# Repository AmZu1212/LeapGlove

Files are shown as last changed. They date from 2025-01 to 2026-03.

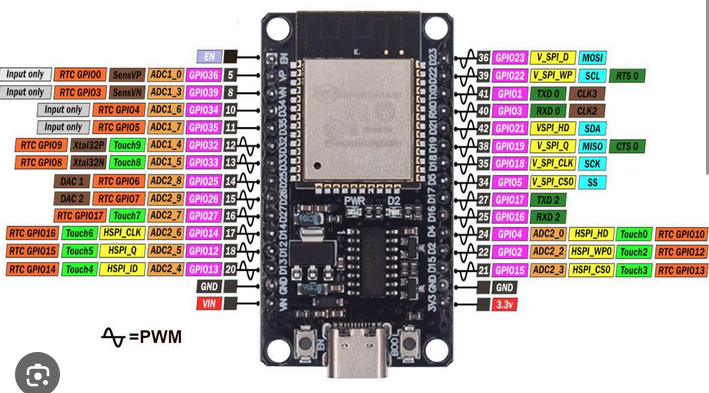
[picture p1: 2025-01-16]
esp pinout.png

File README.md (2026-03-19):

Top Banner
<div align="center">
  <h1>The LeapGlove Project</h1>
  LeapGlove
</div>

## Contact Us
For any questions, feel free to reach out:
- **Emails**: zuabiamir@gmail.com , liz.dushkin@gmail.com
> **Note:** For a complete step-by-step build guide, see the [LeapGlove Wiki Welcome page](https://github.com/AmZu1212/LeapGlove/wiki/%231-Welcome).
  
## Overview
The **LeapGlove Project** aims to repurpose the [LucidGloves](https://github.com/LucidVR/lucidgloves) to control the [LeapHand](https://v1.leaphand.com/) while retaining the haptic feedback capabilities of the glove. 

This initiative focuses on creating an affordable, human-computer interaction interface for the LeapHand.

Watch the showcase here:

Watch the video (https://www.youtube.com/shorts/LX1qnLxFVLc)

The LeapGlove Project builds on:
- **LucidGloves Prototype 4**: [GitHub Repository](https://github.com/LucidVR/lucidgloves)
- **LeapHand API**: [LeapHand Documentation](https://v1.leaphand.com/)

please consider leaving a star on both of the repos above, as without their previous work, this would not be possible.

## Project Objectives
- Repurpose the LucidGloves to function as controllers for the LeapHand.
- Retain the haptic feedback features of the LucidGloves.
- Provide an affordable and accessible solution for LeapHand control.

## Project Status
- This project is finished. We fell abit short of our expected implementation due to the physical design of the mechanism, and due to the latency the servo motors have.
- As a leap hand controller, the gloves supports general finger motion, except fine grain movement and splay movement.
- And for the haptics, it was unfortunately impossible to implement a realtime transmission of haptics, so we created haptic presets from 0% to 90%, so it can be demo'ed if anyone wishes to see how it may feel. 

## Demonstration Videos
- **Glove Demo**:

https://github.com/user-attachments/assets/84f64e34-5cb0-47a1-a268-5b9e06becb94

- **Leap Hand Demo (Courtesy of LeapHand.com)**:

https://github.com/user-attachments/assets/7a54c01e-ebf4-48aa-9cdf-c213115a098e

---

## LeapGlove Assembly & Setup Guide

## Step 1: Complete Hardware List
The hardware needed is listed here, or alternatively you can check lucas'es hadrware list. 
Just be sure to use an `esp32-wroom-32` and not an arduino nano. [Lucas's original parts list](https://github.com/LucidVR/lucidgloves/wiki/Prototype-4-Parts-List)

The Required Hardware:
- 5 black badge reels
- 5 round 10k potentiometers
- 5 mg90s 9g servos
- 1 ESP32-WROOM-32
- 2 small powerbanks (or a power solution of your choice)
- 1 firm-cloth glove (**cloth should not be flexible** for proper haptics)
- Dupont crimp set, crimper, and 28AWG wire kit
- 2 USB-C cables (one for ESP32, one for servos)
- 1 spool of standard PLA/PETG for 3D printing (and a 3D printer)
- 4 M2 bolts and nuts
- Soldering iron and solder
- Foam surface for comfort (to stick under the motor mount base)
- Hot glue gun (even a cheap one will do)
- Some small rope
- A Scotch fishing strap 

> **You will also need a LeapHand already built. See:**  
> [LeapHand Website & CAD Files](https://v1.leaphand.com/leap_cad)

## Step 2: 3D Printing Guide

- Please follow the guide below:  
  [Prototype 4 Printing Guide](https://github.com/LucidVR/lucidgloves/wiki/Prototype-4-Printing-Guide)

- Find the STL files: 
  Navigate to the `lucidglove/3d models` folder in this repository to locate all the required printable parts.  
  > **Note:** Some models differ from the original LucidGlove designs, featuring improvements for print quality and structural strength.

- Check the README in each subfolder:
  Each subfolder contains a `README` file specifying which parts to print and how many of each are needed.

- **Printing Tips:**  
  - Use PLA or PETG for strength and reliability.
  - Recommended infill: at least 20% for durability.
  - Some parts may require supports (snug supports are recommended for all the sliding parts. For the rest use *snug* supports).
  - Test-fit parts before final assembly.

## Step 3: Assembly

Refer to Lucas’s video for a step-by-step assembly:  
Assembly Video (https://www.youtube.com/watch?v=2yF-SJcg3zQ)

**Notes:**
- The majority of the glove’s assembly follows the original LucidGlove design.  
- Use the .stl files we provided (they are more print-friendly than Lucas's designs).
- The motor mounts are designed to be hot glued onto the glove (there is extra space to glue under and on the sides).
- Instead of mounting a Quest2 controller, use the ESP32 mount we provided.

## Step 4: ESP32 Connections

There is flexibility in pin choice if you edit the firmware config.  
This guide assumes you are using the provided firmware as-is (we recommend to not change anything and run as-is).

- The wires should be connected like so:
  
- The finished product should look like this:
  
  
## Step 5: Setting Up the Code

1. **Download CH340 USB drivers:**  
   - [CH340 driver link here](https://sparks.gogo.co.nz/ch340.html)
   - please not that maybe your esp wil have a cp210 driver instead, just install that one.
   - The driver type depends on the small chip near the usb port on the esp board.

2. **Install drivers** and connect your ESP32 board via USB.

3. **Open Windows Device Manager:**
    - Right click the Windows icon  
      
    - Choose Device Manager  
      

    - Find your “CH340” COM device under Ports (COM & LPT). (For us it is COM3, but for you the number may be different) 
      

4. **Download and install Arduino IDE.**  
   Follow Lucas’s video for preparation and board profile setup (use the updated firmware):  
   [Lucas's Arduino Prep Video](https://www.youtube.com/watch?v=2yF-SJcg3zQ)

5. **Compile and program the ESP32.**

6. **Connect the electronics and pair the LeapGlove with Windows via Bluetooth:**
    - Open your PC’s Bluetooth panel and pair with the LeapGlove.
    - Check in device manager which COM# is your esp bluetooth connection:

      
      
    - Update the esp port in the script:
      

## Step 6: How to Wear and Use the Glove Safely

- **Tension will differ per user.**
- **You must:**  
  - Re-tighten the ropes  
  - Adjust the servo motor’s tail

### Rope and Servo Adjustment Procedure

1. Remove all 5 tails from the servos.
2. Run the script, press `Ctrl+C`, and wait for calibration to finish.
3. Press `0` to reset servo positions to zero.  
   Close the script.
4. Tighten and spin the ropes on each finger cap handle.
    - Ensure there is tension even when the hand is fully open.
5. Close your hand.
6. For each motor, one by one, put the tail on **after** (clockwise) the screw position.  
   This sets the motor’s “zero” point. Please refer to the image and gif below:
   
   Motor Tail Placement

   GIF of how it should look like:
   
   Motor Tail Placement GIF

### Operation Safety

- **Always have your hand fully open when changing haptic presets.**  
  - Not doing so may cause the servo tail to hit the brake screw and dislodge it, ruining the haptic mechanism.
- **If you have tracking issues:**  
  - Ropes aren’t tight enough. Re-tighten and recalibrate.
- **If you have haptics issues (servos don’t stop hand movement):**  
  - Glove material is too flexible, or servos are misaligned. Re-align as above.

### Final Steps

- **LeapHand Setup:**  
  Build and connect the LeapHand to your PC following the [LeapHand documentation](https://v1.leaphand.com/).

- **Software:**  
  Once hardware is ready and connected (if used bluetooth dont forget to pair to the LeapGlove), run the integration script for the `Our Files` Folder:
  ```
  python ./LeapGlove.py
  ```

Bottom Banner

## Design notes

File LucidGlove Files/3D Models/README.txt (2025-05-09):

Hello!

Check each folder for what you need to print.
Open "#Print Guide.txt" and check the list and the instructions.

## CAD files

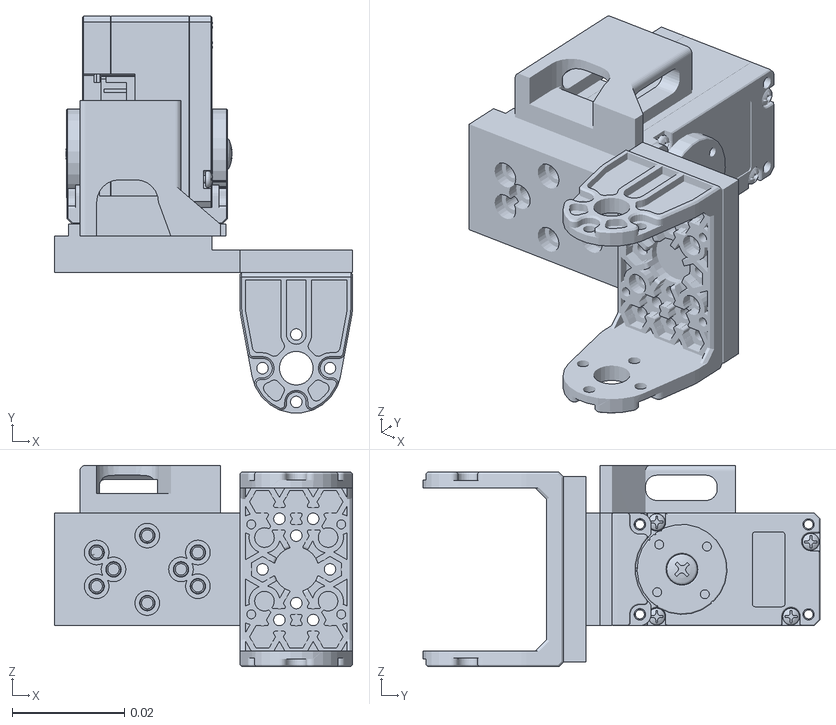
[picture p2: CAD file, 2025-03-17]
LeapHand Files/LeapHand Simulator/assets/leap_hand/mcp_joint.stl
0.053 x 0.0705 x 0.0358

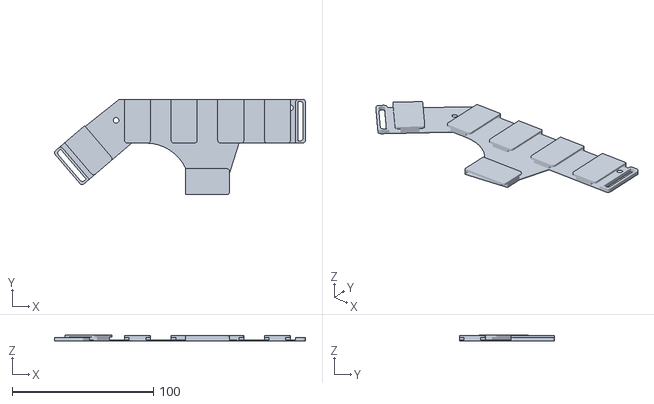
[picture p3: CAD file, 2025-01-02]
LucidGlove Files/3D Models/Base/Right_Hand_Base.stl
177.7 x 67.6 x 4.60

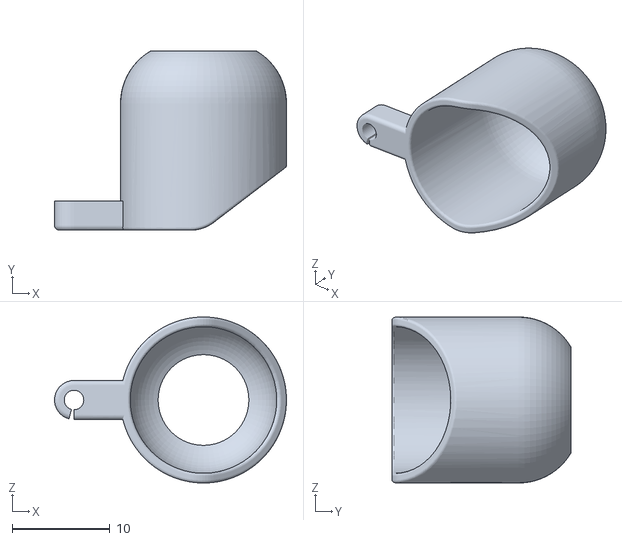
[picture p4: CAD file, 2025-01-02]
LucidGlove Files/3D Models/Fingers/Finger_Cap.stl
23.8 x 18.4 x 17.0

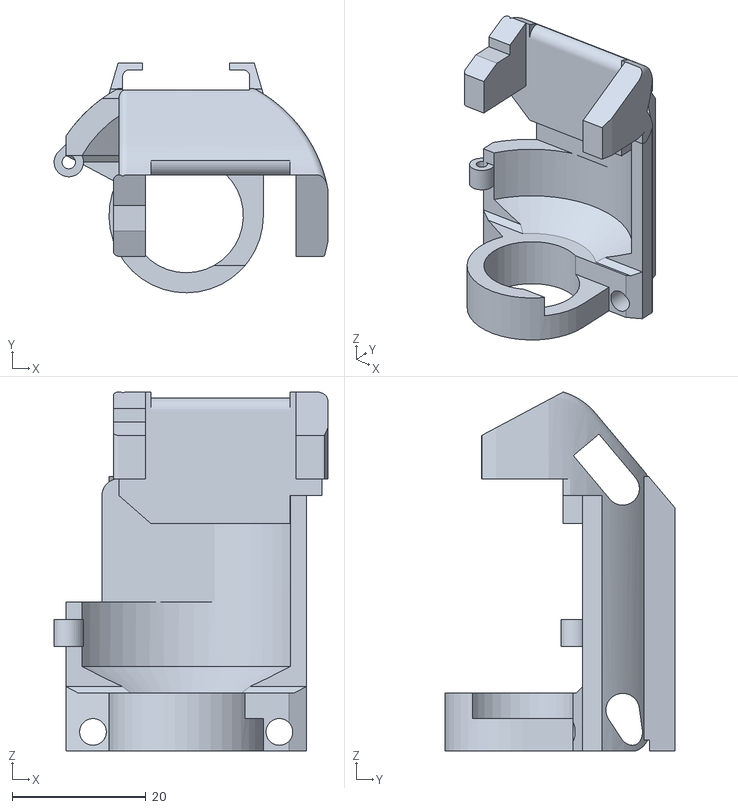
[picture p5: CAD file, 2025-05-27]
LucidGlove Files/3D Models/Mounts/Motor_Mount.stl
41.0 x 34.3 x 53.7

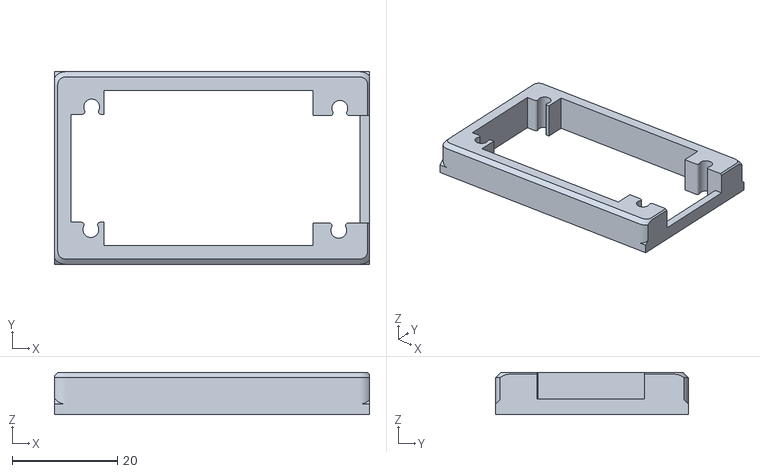
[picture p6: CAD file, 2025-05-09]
LucidGlove Files/3D Models/Mounts/Mount Source Files/ESP_Bracket.stl
59.8 x 36.6 x 8.00

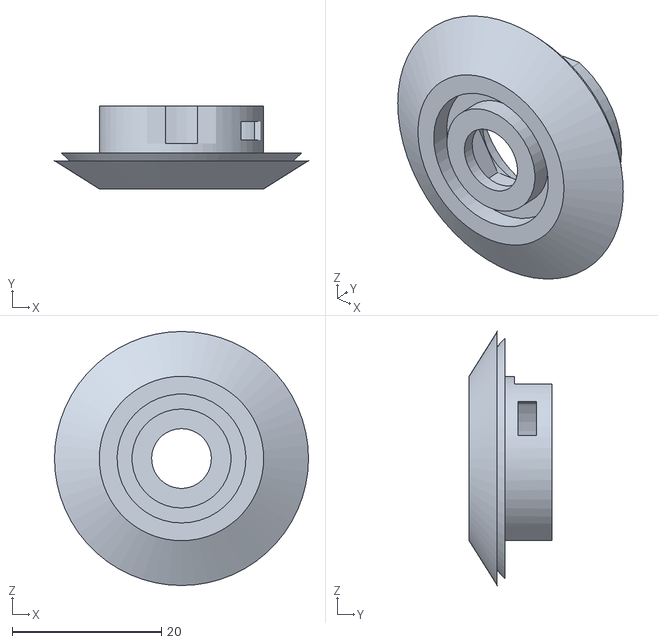
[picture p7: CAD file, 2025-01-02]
LucidGlove Files/3D Models/Spool & Coil/Coil_Holder.stl
34.0 x 11.1 x 34.0

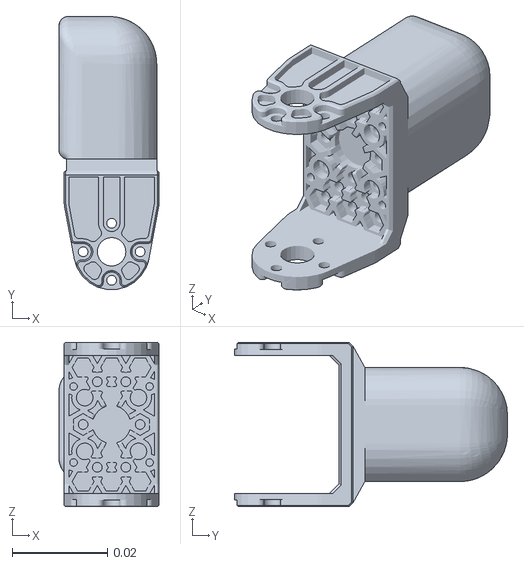
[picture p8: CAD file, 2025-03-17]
LeapHand Files/LeapHand Simulator/assets/leap_hand/fingertip.stl
0.0211 x 0.0574 x 0.0346

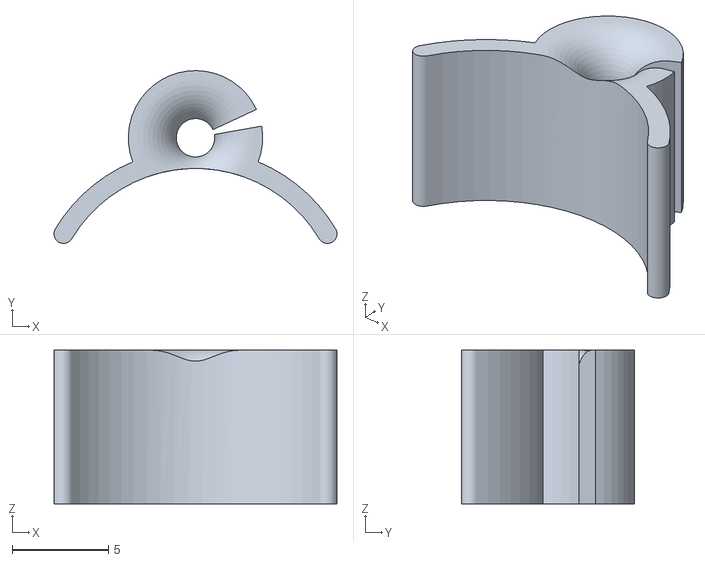
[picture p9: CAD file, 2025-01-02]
LucidGlove Files/3D Models/Fingers/String_Guide.stl
14.7 x 9.00 x 8.00

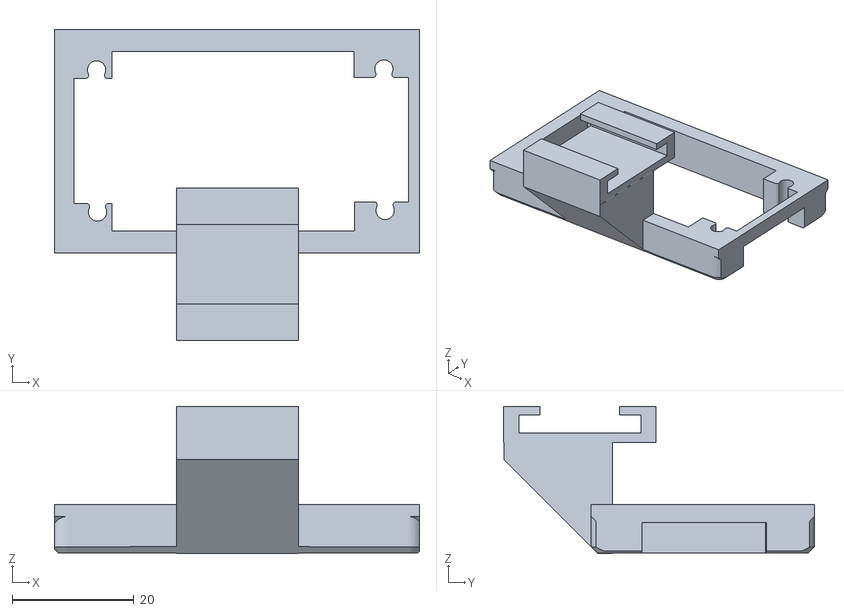
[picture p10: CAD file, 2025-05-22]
LucidGlove Files/3D Models/Mounts/ESP_Mount.stl
59.8 x 50.9 x 24.2

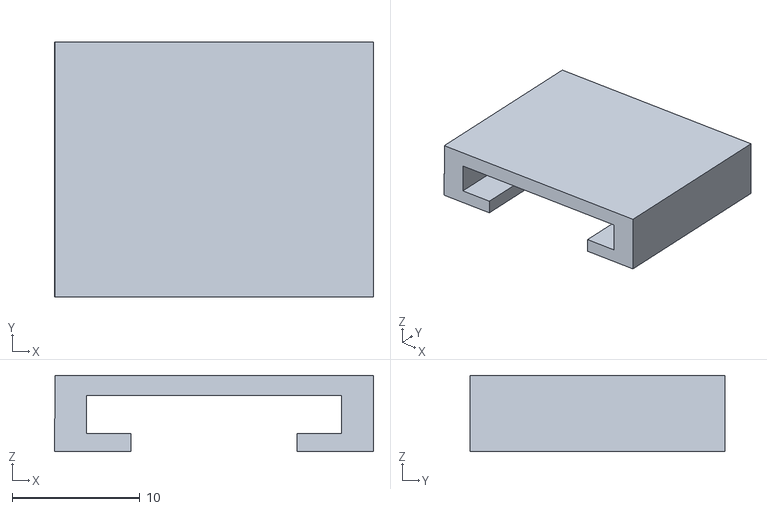
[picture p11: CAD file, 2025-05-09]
LucidGlove Files/3D Models/Mounts/Mount Source Files/Mount_Slide.stl
25.0 x 20.0 x 5.97

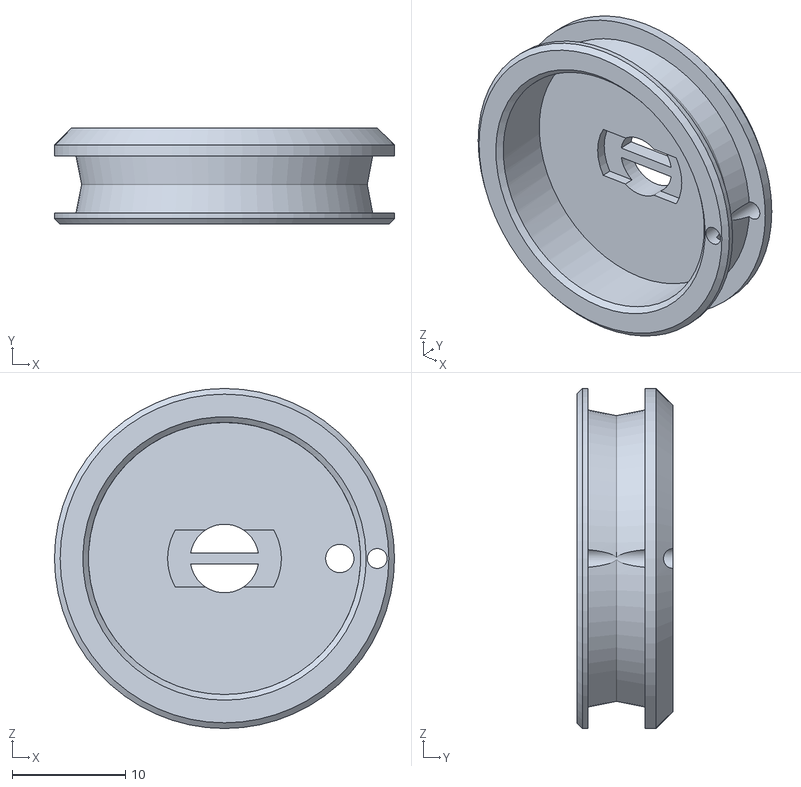
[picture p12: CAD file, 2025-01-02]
LucidGlove Files/3D Models/Spool & Coil/String_Spool.stl
30.0 x 8.50 x 30.0

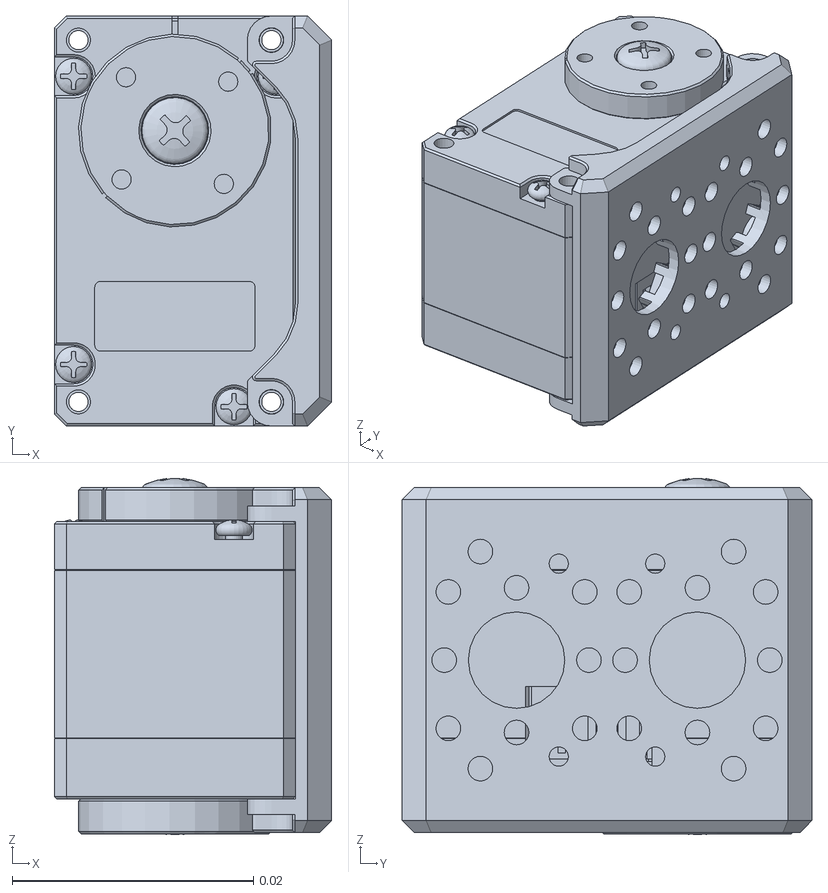
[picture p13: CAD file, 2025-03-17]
LeapHand Files/LeapHand Simulator/assets/leap_hand/pip.stl
0.023 x 0.034 x 0.0295

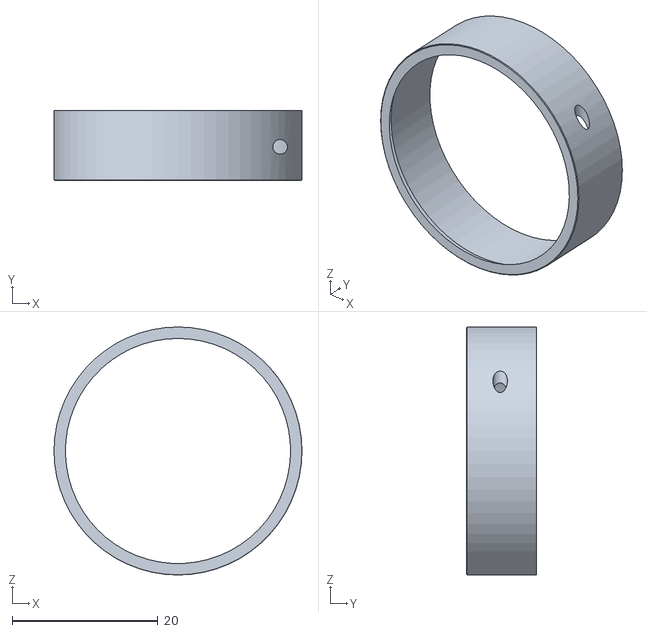
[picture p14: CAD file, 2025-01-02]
LucidGlove Files/3D Models/Spool & Coil/Spool_Ring.stl
34.0 x 9.63 x 34.0

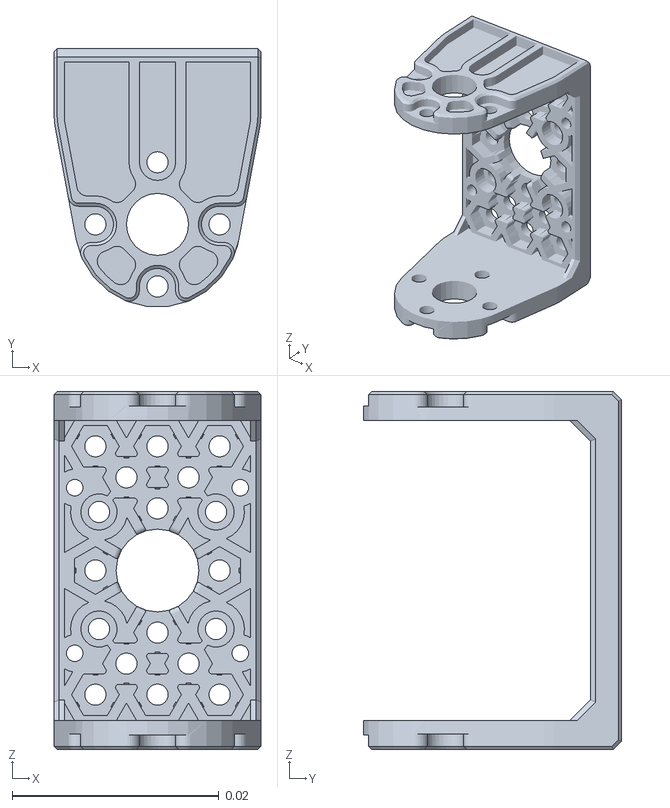
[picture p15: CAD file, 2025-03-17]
LeapHand Files/LeapHand Simulator/assets/leap_hand/thumb_pip.stl
0.02 x 0.0249 x 0.0346

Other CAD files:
LucidGlove Files/3D Models/Base/Left_Hand_Base.stl
LucidGlove Files/3D Models/Mounts/Mount Source Files/Motor_Mount.stl
LeapHand Files/LeapHand Simulator/assets/leap_hand/thumb_dip.stl
LeapHand Files/LeapHand Simulator/assets/leap_hand/dip.stl
LeapHand Files/LeapHand Simulator/assets/leap_hand/thumb_fingertip.stl
LucidGlove Files/3D Models/Mounts/Mount Source Files/Old_ESP_Mount.stl

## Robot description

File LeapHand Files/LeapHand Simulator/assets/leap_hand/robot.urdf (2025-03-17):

<robot name="onshape">
<link name="palm_lower">
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
<inertial>
<origin xyz="0 0 0" rpy="0 0 0"/>
<mass value="0.237" />
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
</inertial>
</link>

<link name="mcp_joint">
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
<inertial>
<origin xyz="0 0 0" rpy="0 0 0"/>
<mass value="0.044" />
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
</inertial>
</link>

<link name="pip">
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
<inertial>
<origin xyz="0 0 0" rpy="0 0 0"/>
<mass value="0.032" />
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
</inertial>
</link>

<link name="dip">
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
<inertial>
<origin xyz="0 0 0" rpy="0 0 0"/>
<mass value="0.037" />
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
</inertial>
</link>

<link name="fingertip">
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
<inertial>
<origin xyz="0 0 0" rpy="0 0 0"/>
<mass value="0.016" />
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
</inertial>
</link>

<joint name="0" type="revolute">
<origin xyz="-0.012200000000000007713 0.038099999999999994982 0.014500000000000000736" rpy="-1.570796326794896558 -1.0065212660796336576e-15 1.5707963267948943376" />
<parent link="mcp_joint" />
<child link="pip" />
<axis xyz="0 0 -1"/>
<limit effort="0.95" velocity="8.48" lower = "-1.047" upper = "1.047"/>
<joint_properties friction="0.0"/>
</joint>

<joint name="1" type="revolute">
<origin xyz="-0.0070952496528625457958 0.023057756134899472233 -0.01872240357846021927" rpy="1.5707963267948950037 1.5707963267948945596 0" />
<parent link="palm_lower" />
<child link="mcp_joint" />
<axis xyz="0 0 -1"/>
<limit effort="0.95" velocity="8.48" lower = "-0.314" upper = "2.23"/>
<joint_properties friction="0.0"/>
</joint>

<joint name="2" type="revolute">
<origin xyz="0.01499999999999996822 0.014299999999999904801 -0.012999999999999824196" rpy="1.5707963267948958919 -1.570796326794896336 0" />
<parent link="pip" />
<child link="dip" />
<axis xyz="0 0 -1"/>
<limit effort="0.95" velocity="8.48" lower = "-0.506" upper = "1.885"/>  
<joint_properties friction="0.0"/>
</joint>

<joint name="3" type="revolute">
<origin xyz="-4.0880582495572692636e-09 -0.036100004210367367397 0.00020000000000007858714" rpy="4.5935029425113685044e-17 -2.8730071914463794583e-16 4.4395481053923607589e-32" />
<parent link="dip" />
<child link="fingertip" />
<axis xyz="0 0 -1"/>
<limit effort="0.95" velocity="8.48" lower = "-0.366" upper = "2.042"/>   
<joint_properties friction="0.0"/>
</joint>

<link name="mcp_joint_2">
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
<inertial>
<origin xyz="0 0 0" rpy="0 0 0"/>
<mass value="0.044" />
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
</inertial>
</link>

<link name="pip_2">
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
<inertial>
<origin xyz="0 0 0" rpy="0 0 0"/>
<mass value="0.032" />
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
</inertial>
</link>

<link name="dip_2">
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
<inertial>
<origin xyz="0 0 0" rpy="0 0 0"/>
<mass value="0.037" />
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
</inertial>
</link>

<link name="fingertip_2">
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
<inertial>
<origin xyz="0 0 0" rpy="0 0 0"/>
<mass value="0.016" />
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
</inertial>
</link>

<joint name="4" type="revolute">
<origin xyz="-0.012200000000000019856 0.038099999999999981104 0.01450000000000000594" rpy="-1.570796326794896558 -1.0065212760057939085e-15 1.5707963267948943376" />
<parent link="mcp_joint_2" />
<child link="pip_2" />
<axis xyz="0 0 -1"/>
<limit effort="0.95" velocity="8.48" lower = "-1.047" upper = "1.047"/>
<joint_properties friction="0.0"/>
</joint>

<joint name="5" type="revolute">
<origin xyz="-0.0070952496528625388569 -0.022392243865100525113 -0.018722403578460229678" rpy="1.570796326794896558 1.570796326794896558 0" />
<parent link="palm_lower" />
<child link="mcp_joint_2" />
<axis xyz="0 0 -1"/>
<limit effort="0.95" velocity="8.48" lower = "-0.314" upper = "2.23"/>
<joint_properties friction="0.0"/>
</joint>

<joint name="6" type="revolute">
<origin xyz="0.014999999999999975159 0.014300000000000000211 -0.013000000000000018485" rpy="1.5707963267948958919 -1.570796326794896336 0" />
<parent link="pip_2" />
<child link="dip_2" />
<axis xyz="0 0 -1"/>
<limit effort="0.95" velocity="8.48" lower = "-0.506" upper = "1.885"/>  
<joint_properties friction="0.0"/>
</joint>

<joint name="7" type="revolute">
<origin xyz="1.0061396160665481148e-16 -0.036099999999999854428 0.00020000000000007858714" rpy="4.5935029425113654229e-17 -2.8730071914463794583e-16 1.4408183216511868558e-31" />
<parent link="dip_2" />
<child link="fingertip_2" />
<axis xyz="0 0 -1"/>
<limit effort="0.95" velocity="8.48" lower = "-0.366" upper = "2.042"/>   
<joint_properties friction="0.0"/>
</joint>

<link name="mcp_joint_3">
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
<inertial>
<origin xyz="0 0 0" rpy="0 0 0"/>
<mass value="0.044" />
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
</inertial>
</link>

<link name="pip_3">
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
<inertial>
<origin xyz="0 0 0" rpy="0 0 0"/>
<mass value="0.032" />
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
</inertial>
</link>

<link name="dip_3">
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
<inertial>
<origin xyz="0 0 0" rpy="0 0 0"/>
<mass value="0.037" />
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
</inertial>
</link>

<link name="fingertip_3">
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
<inertial>
<origin xyz="0 0 0" rpy="0 0 0"/>
<mass value="0.016" />
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
</inertial>
</link>

<joint name="8" type="revolute">
<origin xyz="-0.012200000000000004244 0.038100000000000001921 0.014499999999999999001" rpy="-1.570796326794896558 -1.0065212660796360242e-15 1.5707963267948943376" />
<parent link="mcp_joint_3" />
<child link="pip_3" />
<axis xyz="0 0 -1"/>
<limit effort="0.95" velocity="8.48" lower = "-1.047" upper = "1.047"/>
<joint_properties friction="0.0"/>
</joint>

<joint name="9" type="revolute">
<origin xyz="-0.0070952454426398371343 -0.067842243865100515521 -0.018722407666402932774" rpy="1.5707963267948950037 1.5707963267948945596 0" />
<parent link="palm_lower" />
<child link="mcp_joint_3" />
<axis xyz="0 0 -1"/>
<limit effort="0.95" velocity="8.48" lower = "-0.314" upper = "2.23"/>
<joint_properties friction="0.0"/>
</joint>

<joint name="10" type="revolute">
<origin xyz="0.014999999999999971689 0.014299999999999951639 -0.012999999999999959505" rpy="1.5707963267948958919 -1.570796326794896336 0" />
<parent link="pip_3" />
<child link="dip_3" />
<axis xyz="0 0 -1"/>
<limit effort="0.95" velocity="8.48" lower = "-0.506" upper = "1.885"/>  
<joint_properties friction="0.0"/>
</joint>

<joint name="11" type="revolute">
<origin xyz="9.7144514654701197287e-17 -0.036099999999999868305 0.00020000000000007511769" rpy="4.5935029425113685044e-17 -2.8730071914463799514e-16 1.5565411607615035382e-32" />
<parent link="dip_3" />
<child link="fingertip_3" />
<axis xyz="0 0 -1"/>
<limit effort="0.95" velocity="8.48" lower = "-0.366" upper = "2.042"/>   
<joint_properties friction="0.0"/>
</joint>

<link name="pip_4">
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
<inertial>
<origin xyz="0 0 0" rpy="0 0 0"/>
<mass value="0.032" />
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
</inertial>
</link>

<link name="thumb_pip">
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
<inertial>
<origin xyz="0 0 0" rpy="0 0 0"/>
<mass value="0.003" />
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
</inertial>
</link>

<link name="thumb_dip">
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
<inertial>
<origin xyz="0 0 0" rpy="0 0 0"/>
<mass value="0.038" />
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
</inertial>
</link>

<link name="thumb_fingertip">
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
<inertial>
<origin xyz="0 0 0" rpy="0 0 0"/>
<mass value="0.049" />
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
</inertial>
</link>

<joint name="12" type="revolute">
<origin xyz="-0.069395249652862533996 -0.0012422438651005258004 -0.021622403578460215601" rpy="-8.2381766464939424156e-17 1.5707963267948956698 0" />
<parent link="palm_lower" />
<child link="pip_4" />
<axis xyz="0 0 -1"/>
<limit effort="0.95" velocity="8.48" lower = "-0.349" upper = "2.094"/> 
<joint_properties friction="0.0"/>
</joint>

<joint name="13" type="revolute">
<origin xyz="-2.7755575615628913511e-17 0.014300000000000005415 -0.013000000000000011546" rpy="1.5707963267948958919 -1.570796326794896336 0" />
<parent link="pip_4" />
<child link="thumb_pip" />
<axis xyz="0 0 -1"/>
<limit effort="0.95" velocity="8.48" lower = "-0.47" upper = "2.443"/> 
<joint_properties friction="0.0"/>
</joint>

<joint name="14" type="revolute">
<origin xyz="0 0.014499999999999966041 -0.017000000000000053263" rpy="-1.570796326794896558 1.6050198443300131245e-46 -1.9721522630516624601e-31" />
<parent link="thumb_pip" />
<child link="thumb_dip" />
<axis xyz="0 0 -1"/>
<limit effort="0.95" velocity="8.48" lower = "-1.20" upper = "1.90"/> 
<joint_properties friction="0.0"/>
</joint>
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

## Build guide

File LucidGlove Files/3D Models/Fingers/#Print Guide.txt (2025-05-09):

Print:

9x String_Guide.stl
5x Finger_Cap.stl

Re-size Finger_Cap.stl to fit each of your fingers. Play with the scale.

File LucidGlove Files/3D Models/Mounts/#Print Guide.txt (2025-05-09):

Print:

5x Motor_Mount.stl
1x ESP_Mount.stl

You can ignore the "Mount Source Files" folder.

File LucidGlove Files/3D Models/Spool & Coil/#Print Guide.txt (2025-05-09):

Print:

5x Coil_Holder.stl
5x Spool_Ring.stl
5x String_Spool.stl

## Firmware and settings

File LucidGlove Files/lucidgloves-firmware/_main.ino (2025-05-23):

#define ALWAYS_CALIBRATING CALIBRATION_LOOPS == -1

#define CALIB_OVERRIDE false
#if USING_CALIB_PIN && COMMUNICATION == COMM_SERIAL && PIN_CALIB == 0 && !CALIB_OVERRIDE
#error "You can't set your calibration pin to 0 over usb. You can calibrate with the BOOT button when using bluetooth only. Set CalibOverride to true to override this."
#endif

ICommunication* comm;
int loops = 0;
void setup() {
#if COMMUNICATION == COMM_SERIAL
  comm = new SerialCommunication();
#elif COMMUNICATION == COMM_BTSERIAL
  comm = new BTSerialCommunication();
#endif
  comm->start();

  setupInputs();

#if USING_FORCE_FEEDBACK
  setupServoHaptics();
#endif
}

void loop() {
  if (comm->isOpen()) {
#if USING_CALIB_PIN
    bool calibButton = getButton(PIN_CALIB) != INVERT_CALIB;
    if (calibButton)
      loops = 0;
#else
    bool calibButton = false;
#endif

    bool calibrate = false;
    if (loops < CALIBRATION_LOOPS || ALWAYS_CALIBRATING) {
      calibrate = true;
      loops++;
    }

    int* fingerPos = getFingerPositions(calibrate, calibButton);
    bool joyButton = getButton(PIN_JOY_BTN) != INVERT_JOY;

#if TRIGGER_GESTURE
    bool triggerButton = triggerGesture(fingerPos);
#else
    bool triggerButton = getButton(PIN_TRIG_BTN) != INVERT_TRIGGER;
#endif

    bool aButton = getButton(PIN_A_BTN) != INVERT_A;
    bool bButton = getButton(PIN_B_BTN) != INVERT_B;

#if GRAB_GESTURE
    bool grabButton = grabGesture(fingerPos);
#else
    bool grabButton = getButton(PIN_GRAB_BTN) != INVERT_GRAB;
#endif

#if PINCH_GESTURE
    bool pinchButton = pinchGesture(fingerPos);
#else
    bool pinchButton = getButton(PIN_PNCH_BTN) != INVERT_PINCH;
    z
#endif

    bool menuButton = getButton(PIN_MENU_BTN) != INVERT_MENU;

    comm->output(encode(fingerPos, getJoyX(), getJoyY(), joyButton, triggerButton, aButton, bButton, grabButton, pinchButton, calibButton, menuButton));
    #if USING_FORCE_FEEDBACK
    static unsigned long lastHapticTime = 0;
    const unsigned long hapticInterval = 15;  // ~66 Hz

    char received[50];
    if (comm->available() && millis() - lastHapticTime > hapticInterval) {
      if (comm->readData(received)) {
        int hapticLimits[5];
        decodeData(received, hapticLimits);
        writeServoHaptics(hapticLimits);
        lastHapticTime = millis();
      }
    }
#endif
    delay(LOOP_TIME);
  }
}

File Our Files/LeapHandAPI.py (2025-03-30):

import numpy as np

from leap_hand_utils.dynamixel_client import *
import leap_hand_utils.leap_hand_utils as lhu
import time
#######################################################
"""This can control and query the LEAP Hand

I recommend you only query when necessary and below 90 samples a second.  Used the combined commands if you can to save time.  Also don't forget about the USB latency settings in the readme.

#Allegro hand conventions:
#0.0 is the all the way out beginning pose, and it goes positive as the fingers close more and more.

#LEAP hand conventions:
#180 is flat out home pose for the index, middle, ring, finger MCPs.
#Applying a positive angle closes the joints more and more to curl closed.
#The MCP is centered at 180 and can move positive or negative to that.

#The joint numbering goes from Index (0-3), Middle(4-7), Ring(8-11) to Thumb(12-15) and from MCP Side, MCP Forward, PIP, DIP for each finger.
#For instance, the MCP Side of Index is ID 0, the MCP Forward of Ring is 9, the DIP of Ring is 11

"""
########################################################
class LeapNode:
    def __init__(self):
        ####Some parameters
        # I recommend you keep the current limit from 350 for the lite, and 550 for the full hand
        # Increase KP if the hand is too weak, decrease if it's jittery.
        self.kP = 600
        self.kI = 0
        self.kD = 200
        self.curr_lim = 350
        self.prev_pos = self.pos = self.curr_pos = lhu.allegro_to_LEAPhand(np.zeros(16))
        #You can put the correct port here or have the node auto-search for a hand at the first 3 ports.
        # For example ls /dev/serial/by-id/* to find your LEAP Hand. Then use the result.  
        # For example: /dev/serial/by-id/usb-FTDI_USB__-__Serial_Converter_FT7W91VW-if00-port0
        self.motors = motors = [0,1,2,3,4,5,6,7,8,9,10,11,12,13,14,15]
        try:
            self.dxl_client = DynamixelClient(motors, '/dev/ttyUSB0', 4000000)
            self.dxl_client.connect()
        except Exception:
            try:
                self.dxl_client = DynamixelClient(motors, '/dev/ttyUSB1', 4000000)
                self.dxl_client.connect()
            except Exception:
                self.dxl_client = DynamixelClient(motors, 'COM5', 4000000)
                self.dxl_client.connect()
        #Enables position-current control mode and the default parameters, it commands a position and then caps the current so the motors don't overload
        self.dxl_client.sync_write(motors, np.ones(len(motors))*5, 11, 1)
        self.dxl_client.set_torque_enabled(motors, True)
        self.dxl_client.sync_write(motors, np.ones(len(motors)) * self.kP, 84, 2) # Pgain stiffness     
        self.dxl_client.sync_write([0,4,8], np.ones(3) * (self.kP * 0.75), 84, 2) # Pgain stiffness for side to side should be a bit less
        self.dxl_client.sync_write(motors, np.ones(len(motors)) * self.kI, 82, 2) # Igain
        self.dxl_client.sync_write(motors, np.ones(len(motors)) * self.kD, 80, 2) # Dgain damping
        self.dxl_client.sync_write([0,4,8], np.ones(3) * (self.kD * 0.75), 80, 2) # Dgain damping for side to side should be a bit less
        #Max at current (in unit 1ma) so don't overheat and grip too hard #500 normal or #350 for lite
        self.dxl_client.sync_write(motors, np.ones(len(motors)) * self.curr_lim, 102, 2)
        self.dxl_client.write_desired_pos(self.motors, self.curr_pos)

    #Receive LEAP pose and directly control the robot
    def set_leap(self, pose):
        self.prev_pos = self.curr_pos
        self.curr_pos = np.array(pose)
        self.dxl_client.write_desired_pos(self.motors, self.curr_pos)
    #allegro compatibility joint angles.  It adds 180 to make the fully open position at 0 instead of 180
    def set_allegro(self, pose):
        pose = lhu.allegro_to_LEAPhand(pose, zeros=False)
        self.prev_pos = self.curr_pos
        self.curr_pos = np.array(pose)
        self.dxl_client.write_desired_pos(self.motors, self.curr_pos)
    #Sim compatibility for policies, it assumes the ranges are [-1,1] and then convert to leap hand ranges.
    def set_ones(self, pose):
        pose = lhu.sim_ones_to_LEAPhand(np.array(pose))
        self.prev_pos = self.curr_pos
        self.curr_pos = np.array(pose)
        self.dxl_client.write_desired_pos(self.motors, self.curr_pos)
    #read position of the robot
    def read_pos(self):
        return self.dxl_client.read_pos()
    #read velocity
    def read_vel(self):
        return self.dxl_client.read_vel()
    #read current
    def read_cur(self):
        return self.dxl_client.read_cur()
    #These combined commands are faster FYI and return a list of data
    def pos_vel(self):
        return self.dxl_client.read_pos_vel()
    #These combined commands are faster FYI and return a list of data
    def pos_vel_eff_srv(self):
        return self.dxl_client.read_pos_vel_cur()
########################################################


#init the node
def main(**kwargs):
    leap_hand = LeapNode()
    while True:
        #Set to an open pose and read the joint angles 33hz
        leap_hand.set_allegro(np.zeros(16))
        print("Position: " + str(leap_hand.read_pos()))
        time.sleep(0.03)

if __name__ == "__main__":
    main()

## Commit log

2025-01-02 Added LucidGloves files
    [ESP32_Wroom_Holder_Desoldered_JST.STL, GreenPotElasticHolder.stl, GreenPotElasticHolder_Proto4.1.STL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]
2025-01-16 added pnout, passed bluetooth serial test. nex tstep is to convert data to finger %
2025-01-26 Added finger % in the python parser! next sttep is to api it to the leap glove
2025-01-31 added sim files
    [ball.urdf, cube.urdf, dip.stl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]
2025-03-30 switched to allegro movement. finger tracking works now. tune needed
2025-04-06 some haptic fixes and servo testing
    [SerialBTCommunication.ino, _main.ino, lucidgloves-firmware.ino]
2025-04-30 bunch if debbuging and corrections. some cutting up code. finger mapping is abit off with the servo commands. this is circumventable.
    [LeapGlove.py, _main.ino, haptics.ino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]
2025-05-09 3D Print File Cleanup and Organization
    [Coil_Holder.stl, ESP32_Wroom_Holder_Desoldered_JST.STL, Finger_Cap.stl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]
2025-05-09 More 3D Print File Changes
    [ESP_Bracket.stl, ESP_Mount.stl, Mount_Slide.stl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]
2025-05-20 updated finger servo mapping comment
2025-05-22 fixed stupid servo race condition
    [SerialBTCommunication.ino, ServoMovementTest.py, _main.ino]
2025-05-22 new esp mount
    [ESP_Mount.stl, Old_ESP_Mount.stl]
2025-05-22 new servo test
2025-05-23 servo fixes & preset basics
    [LeapGlove.py, ServoMovementTest.py, _main.ino]
2025-05-27 updated motor stl
    [Motor_Mount.stl]
2025-06-05 moved showcase higher in landing page
